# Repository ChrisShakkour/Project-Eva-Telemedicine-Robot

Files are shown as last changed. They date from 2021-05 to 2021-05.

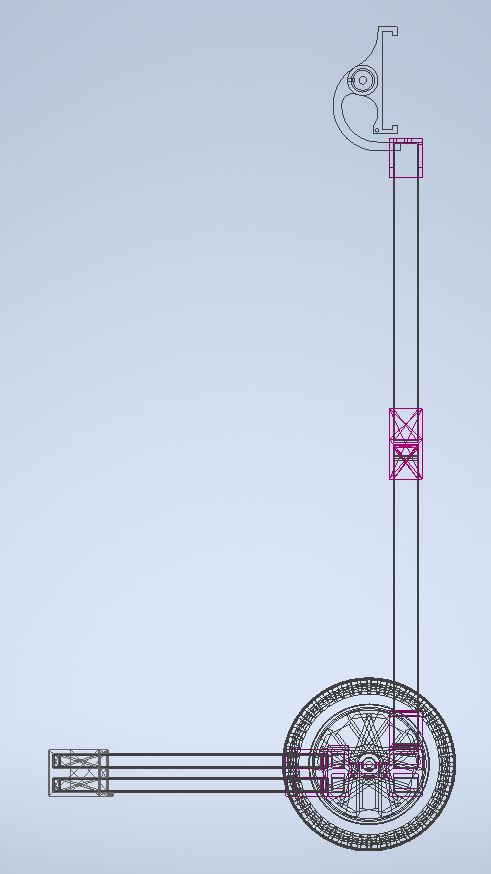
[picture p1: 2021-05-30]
Mechanical design/pictures/Capture2.JPG

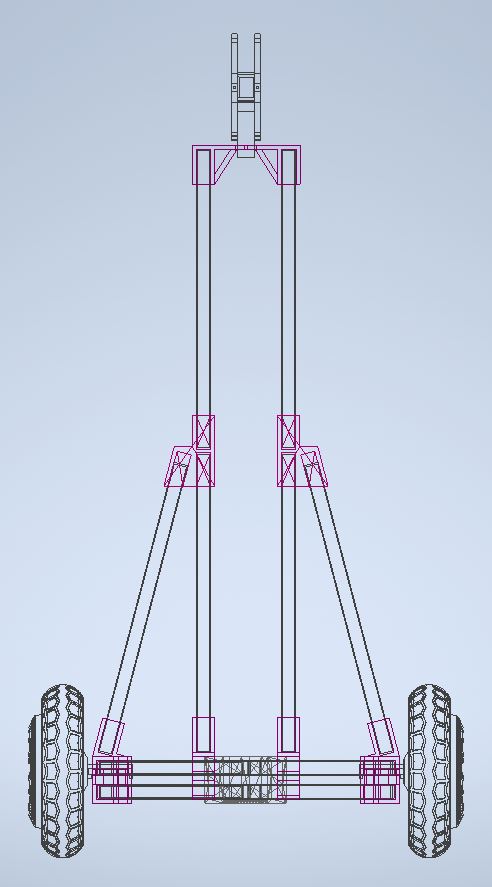
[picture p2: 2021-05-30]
Mechanical design/pictures/Capture1.JPG

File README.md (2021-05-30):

# Project Eva Telemedicine Robot

## Abstract
Telemedicine or Telehealth is the distribution of health-related services and information via 
electronic information and telecommunication technologies. It allows long-distance patient and 
clinician contact, care, advice, reminders, education, intervention, monitoring, and remote 
admissions. In this project we aim to build an easy to use, yet intelligent Robot assistant that will 
serve as a RC gateway between long distance patients and their families, doctors, loved ones
providing the patient with care, monitoring, & Telemedicine. The robot itself is a 3-wheel
differential drive robot built on a 3D printed chassis and a STM32F407VET microcontroller 
Featuring an Arm-Cortex-M4 168[MHz] Core. The robot is equipped with a mobile device 
(Tablet) to enable video conferencing. anyone with permissions can call the robot and remote 
control it from far away to monitor the patient/family member. The robot built in this project 
fully occupies these features, calling the robot from far away and driving in the patient’s home 
to firstly check on him and secondly check on his health and satisfaction, our conclusions from 
this robot are, firstly this concept could be implemented into a real life product with many use 
cases, secondly it is a product customers would like to use but don’t have the will to purchase 
because cheaper solutions can bring the same results at zero investment like using a 
smartphone to video conference, Etc.

## Project overview
Project EVA is a combination of 2 systems, an embedded real-time Robot system & an IoT 
software agent. the Robot system is independently handled with a microcontroller equipped 
with sensors, power distribution & management components, a camera, and an intelligent Real￾time software, whereas the IoT agent is built upon 2 applications running on different mobile 
devices connected via a firebase. The Robotic system receives commands from the IoT software 
agent via a Bluetooth wireless communication protocol.

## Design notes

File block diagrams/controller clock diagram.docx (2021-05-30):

Motor

Motor

BLDC motor drivers

BLDC motor drivers

PWM

PWM

Microcontroller

I2C

Capture compare

UART

SPI

Proximity sensors

Bluetooth module HC-05

Pixy camera

Accelerometer

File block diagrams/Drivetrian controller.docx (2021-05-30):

Left wheel speed

Right wheel speed

Radios of Arc

Speed

Drivetrain controller

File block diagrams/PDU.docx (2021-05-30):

Battery input voltage

14v-16.5v

PDU

Servo + proximity sensors circuit

Microcontroller

Pixy camera

14v-16.5v

5V

6V

BLDC Motor Driver

Min 14v

BLDC Motor Driver

Min 14v

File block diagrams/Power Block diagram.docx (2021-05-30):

14v-16v

6V

5V

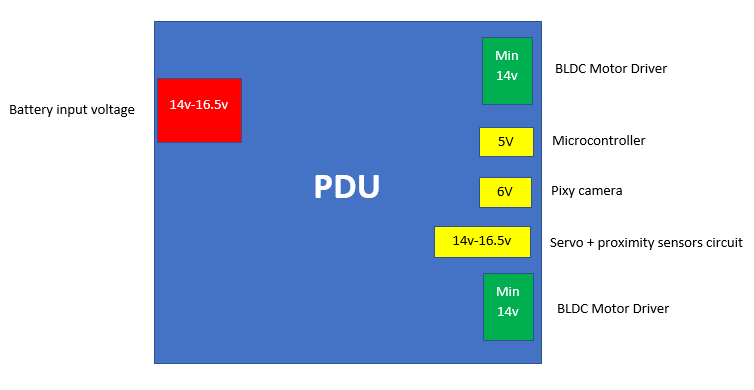
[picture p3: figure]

Sensory

Pixy Cam

Microcontroller

Power

BLDC motor driver

Power

BLDC motor driver

Battery 14v-16.5v

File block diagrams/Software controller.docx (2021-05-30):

Embedded Software controller

LWS

RWS

Speed

Radios

Gaussian transform

Speed

angle

Drivetrain controller

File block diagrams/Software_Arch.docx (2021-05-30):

External interrupt

Interrupt free

50ms

20ms

Bluetooth message handler

Kinematics controller

Scheduler

Main

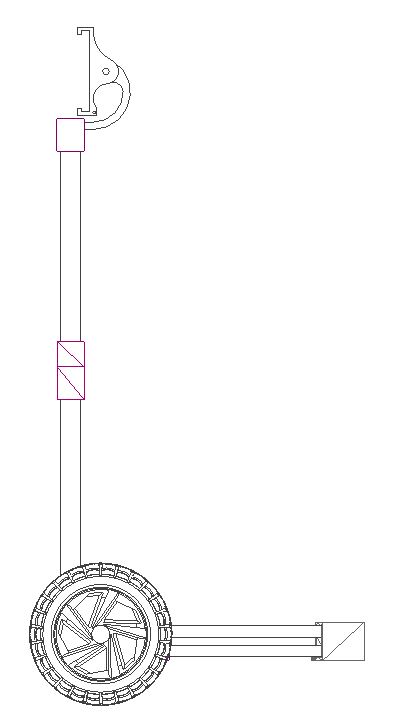
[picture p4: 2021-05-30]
Mechanical design/pictures/Capture10.JPG

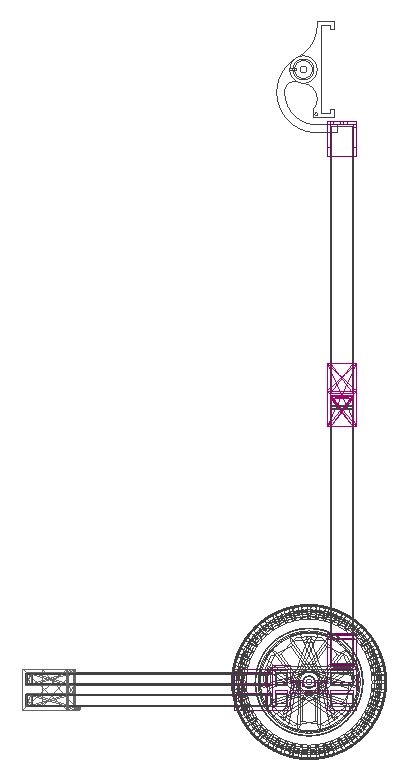
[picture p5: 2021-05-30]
Mechanical design/pictures/Capture5.JPG

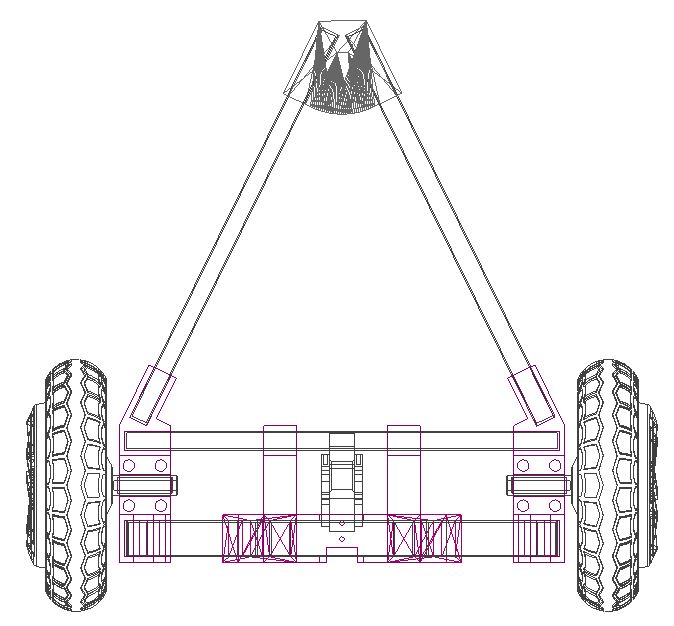
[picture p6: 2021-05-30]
Mechanical design/pictures/Capture7.JPG

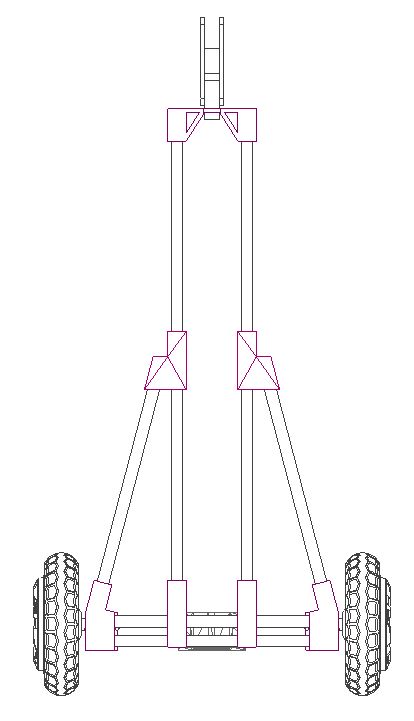
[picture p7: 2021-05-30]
Mechanical design/pictures/Capture12.JPG

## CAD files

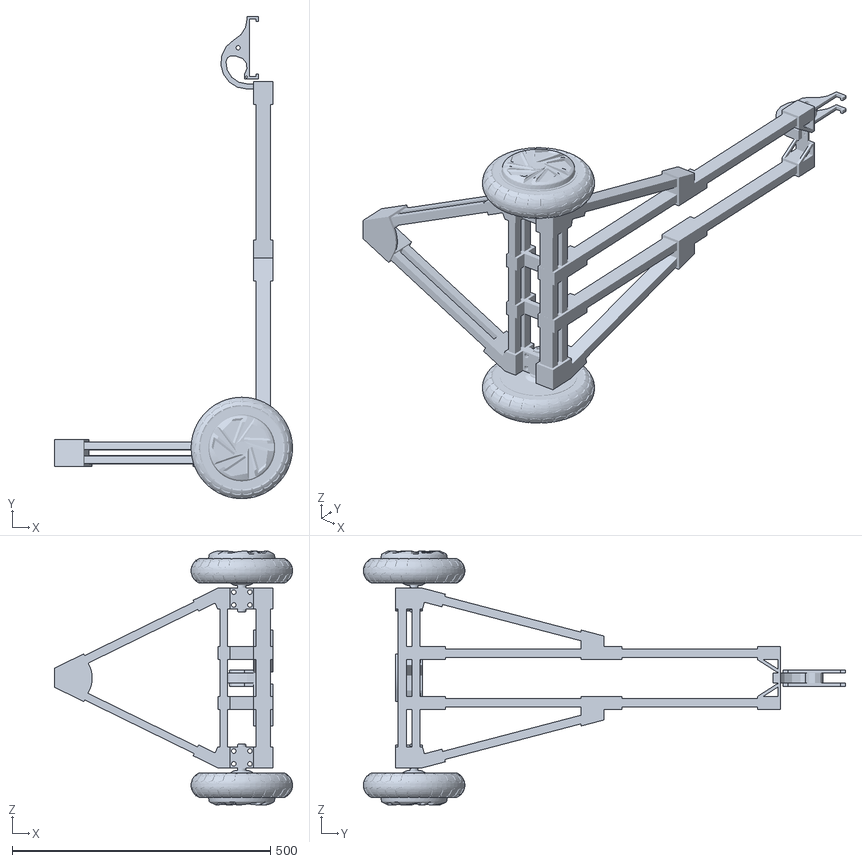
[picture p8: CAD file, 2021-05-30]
Mechanical design/Design sources/DriveTrain_Assembly.stl
461.3 x 934.3 x 492.2

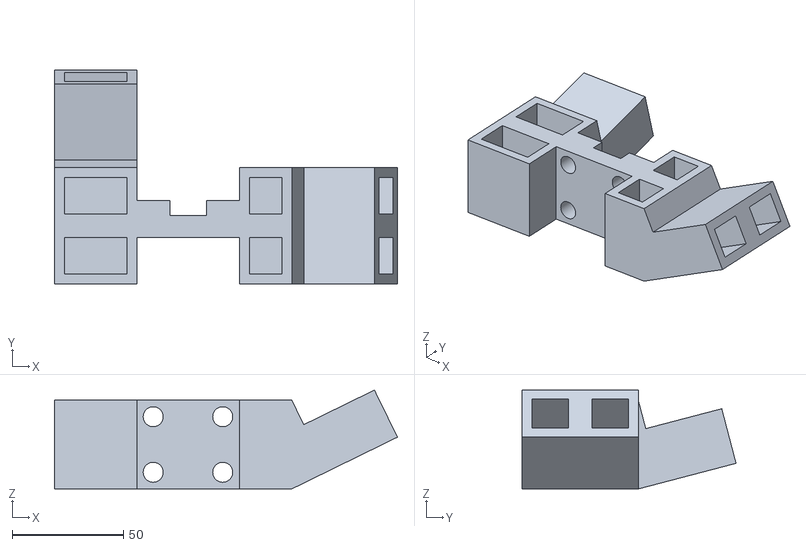
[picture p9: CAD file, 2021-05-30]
Mechanical design/Design sources/STL files/Right_front_Chasis_v2.stl
154.4 x 96.4 x 44.5

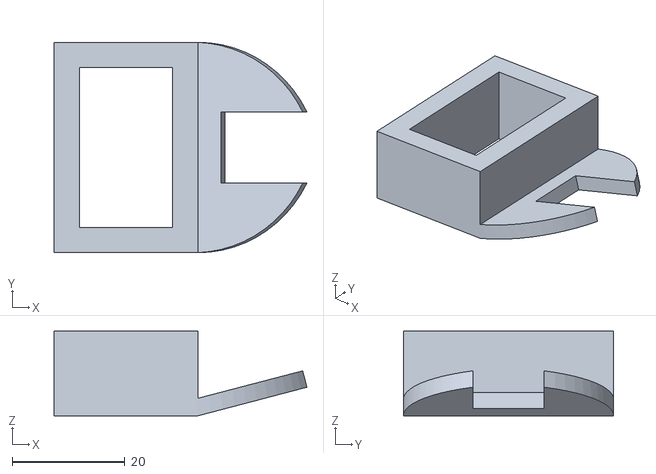
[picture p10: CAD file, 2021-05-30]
Mechanical design/Design sources/STL files/Servo front rightleft holder.stl
44.8 x 37.3 x 15.0

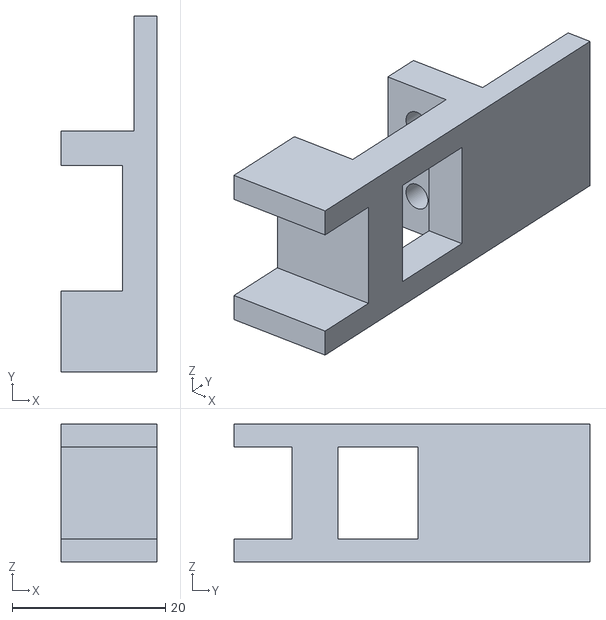
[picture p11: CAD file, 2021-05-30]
Mechanical design/Design sources/STL files/pixyCam_mount.stl
12.5 x 46.5 x 18.0

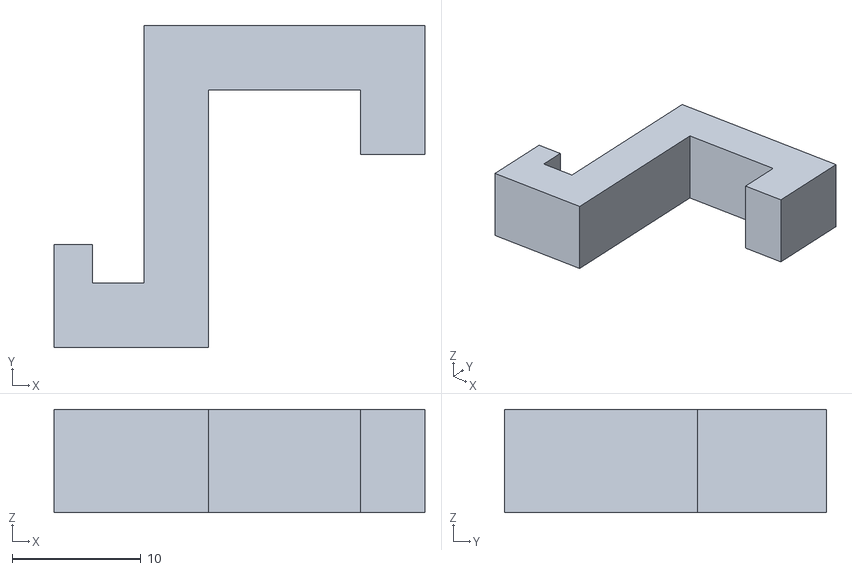
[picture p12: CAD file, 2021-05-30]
Mechanical design/Design sources/STL files/horizontal_clip.stl
28.8 x 25.0 x 8.00

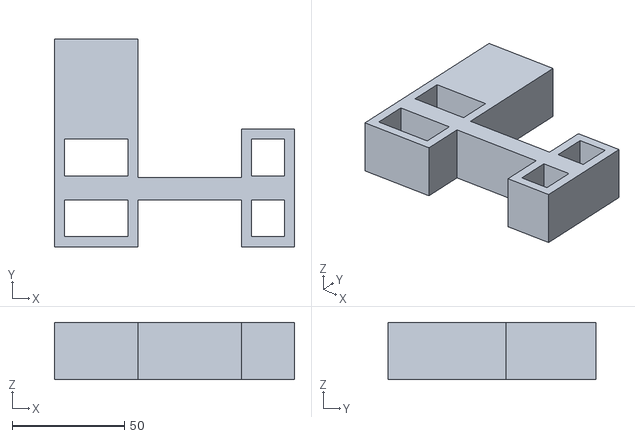
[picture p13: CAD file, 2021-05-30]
Mechanical design/Design sources/STL files/mid_front_Chasis.stl
106.8 x 92.4 x 25.4

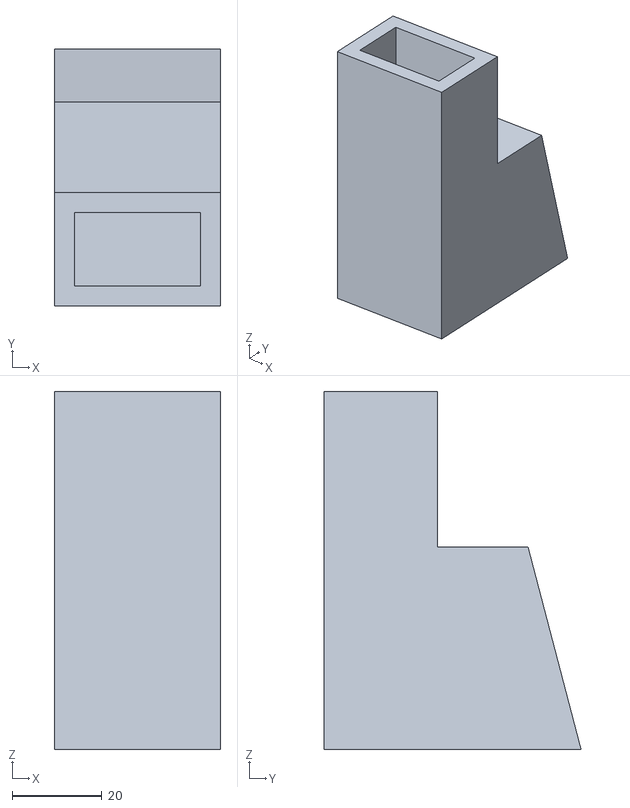
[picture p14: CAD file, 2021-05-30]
Mechanical design/Design sources/STL files/upper_joints.stl
37.2 x 57.5 x 80.0

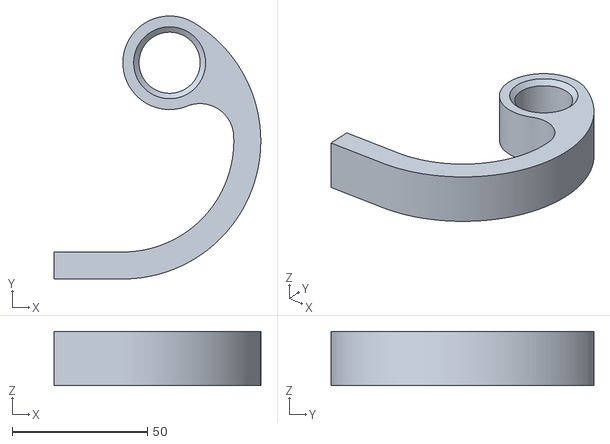
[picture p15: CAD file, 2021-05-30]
Mechanical design/Design sources/STL files/tablet_arm_joint.stl
76.4 x 97.3 x 20.0

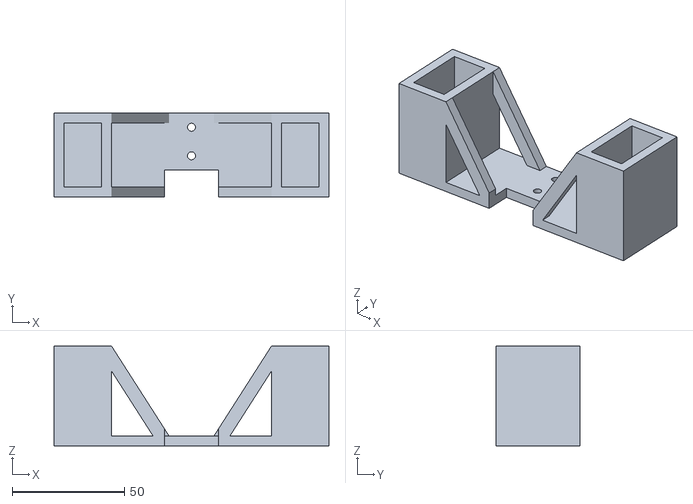
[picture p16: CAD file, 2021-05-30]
Mechanical design/Design sources/STL files/Tablet_joint_Holder.stl
122.4 x 37.4 x 44.5

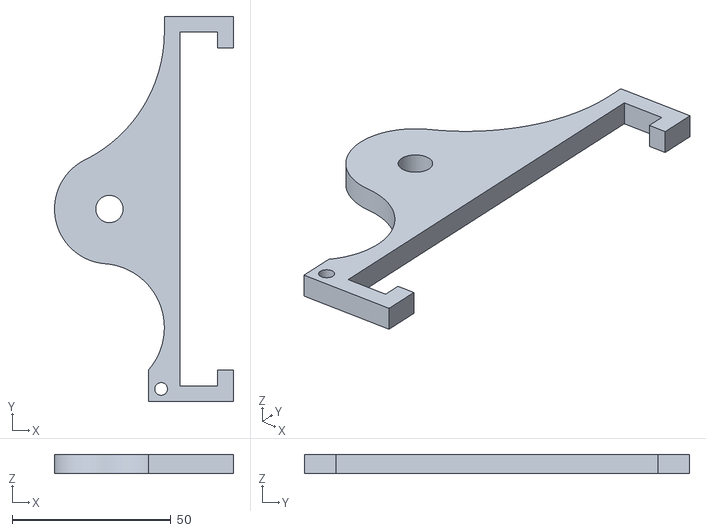
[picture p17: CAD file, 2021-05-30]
Mechanical design/Design sources/STL files/tab_clips.stl
56.4 x 121.4 x 6.00

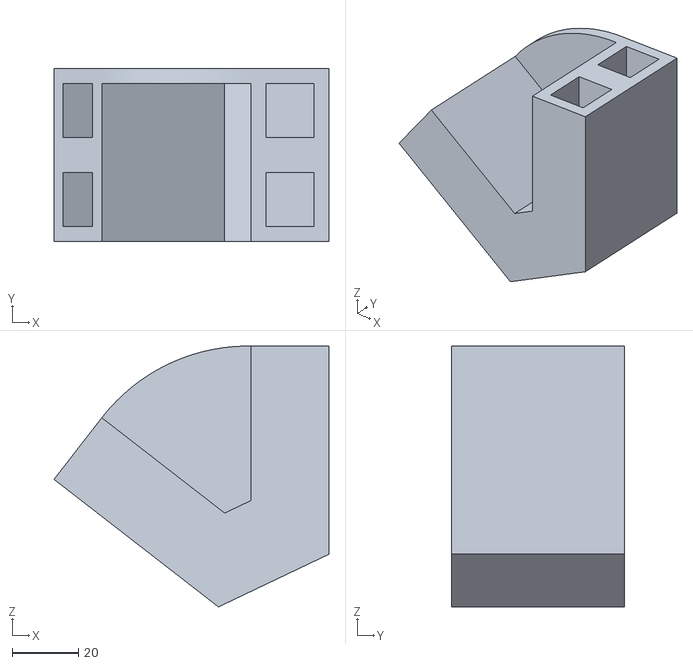
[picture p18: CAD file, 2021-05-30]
Mechanical design/Design sources/STL files/backwheel_Mount.stl
83.2 x 52.4 x 79.0

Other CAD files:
Mechanical design/Design sources/STL files/Left_front_Chasis_v2.stl
Mechanical design/Design sources/DriveTrain_Assembly.iam
Mechanical design/Design sources/Inventor files/Left_front_Chasis_v2.ipt
Mechanical design/Design sources/Inventor files/Motor_BLDC_Hoverboard_Wheel.ipt
Mechanical design/Design sources/Inventor files/PL_rod_double.ipt
Mechanical design/Design sources/Inventor files/PL_rod_single.ipt
Mechanical design/Design sources/Inventor files/Right_front_Chasis_v2.ipt
Mechanical design/Design sources/Inventor files/Servo front rightleft holder.ipt
Mechanical design/Design sources/Inventor files/Tablet_joint_Holder.ipt
Mechanical design/Design sources/Inventor files/backwheel.ipt
Mechanical design/Design sources/Inventor files/backwheel_Cap.ipt
Mechanical design/Design sources/Inventor files/backwheel_Mount.ipt
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

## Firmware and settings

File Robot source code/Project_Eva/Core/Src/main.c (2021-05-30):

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
/* Includes ------------------------------------------------------------------*/
#include "main.h"

I2C_HandleTypeDef hi2c2;

SPI_HandleTypeDef hspi1;

TIM_HandleTypeDef htim2;
TIM_HandleTypeDef htim3;
TIM_HandleTypeDef htim4;
TIM_HandleTypeDef htim6;
TIM_HandleTypeDef htim10;

UART_HandleTypeDef huart1;

void SystemClock_Config(void);
static void MX_GPIO_Init(void);
static void MX_TIM2_Init(void);
static void MX_I2C2_Init(void);
static void MX_SPI1_Init(void);
static void MX_USART1_UART_Init(void);
static void MX_TIM4_Init(void);
static void MX_TIM6_Init(void);
static void MX_TIM10_Init(void);
static void MX_TIM3_Init(void);
/* USER CODE BEGIN 0 */
	uint8_t inbuffer2[30] = {0};
	Pixy2_Data_CCC Signature_1;
	Pixy2_Data_LTC Barcode;
/* USER CODE END 0 */

/**
  * @brief  The application entry point.
  * @retval int
  */
int main(void)
{
  /* MCU Configuration--------------------------------------------------------*/

  /* Reset of all peripherals, Initializes the Flash interface and the Systick. */
  HAL_Init();

  /* Configure the system clock */
  SystemClock_Config();

  /* Initialize all configured peripherals */
  MX_GPIO_Init();
  MX_TIM2_Init();
  MX_I2C2_Init();
  MX_SPI1_Init();
  MX_USART1_UART_Init();
  MX_TIM4_Init();
  MX_TIM6_Init();
  MX_TIM10_Init();
  MX_TIM3_Init();
  /* USER CODE BEGIN 2 */
  calculate_Gaussian_Transform();
  //.set LED off:
  HAL_GPIO_WritePin(GPIOA, LED2_Pin, 0);
  //.general IO initializations:
  HAL_TIM_Base_Start_IT(&htim6);				//initiate scheduler timer 20ms period
  HAL_TIM_Base_Start_IT(&htim2);				//initiate Motor Drive control Timer 0.5ms period
  //.start UART Engine on interrupt mode:
  __HAL_UART_ENABLE_IT(&huart1, UART_IT_RXNE);	//initiate hsuart interrupt on rx

  //.setup MPU6050 Sensor:
  MPU6050_Init(&hi2c2);
  MPU_ConfigTypeDef MPU6050IMU ;
  MPU6050IMU.Accel_Full_Scale = AFS_SEL_2g;
  MPU6050IMU.CONFIG_DLPF = DLPF_184A_188G_Hz;
  MPU6050IMU.ClockSource = Internal_8MHz;
  MPU6050IMU.Gyro_Full_Scale = FS_SEL_250;
  MPU6050IMU.Sleep_Mode_Bit = 0;
  MPU6050_Config(&MPU6050IMU);
  RawData_Def Accel_Raw_Cali;
  MPU6050_Get_Accel_RawData(&Accel_Raw_Cali);
  // ************************
  Enable_Motor('R');
  Enable_Motor('L');
  Initiate_PWM_Signal('R');
  Initiate_PWM_Signal('L');
  Set_Right_Motor_Direction('F');
  Set_Left_Motor_Direction('F');

  HAL_TIM_PWM_Start(&htim3, TIM_CHANNEL_1);
  //HAL_TIM_PWM_Start(&htim3, TIM_CHANNEL_2);
  //HAL_TIM_PWM_Start(&htim3, TIM_CHANNEL_3);
  //HAL_TIM_PWM_Start(&htim3, TIM_CHANNEL_4);

  //htim3.Instance -> CCR1= (180+0)  ;
  //htim3.Instance -> CCR1= (180+90)  ;
  //htim3.Instance -> CCR1= (180+180)  ;
  //htim3.Instance -> CCR1= (180+45)  ;
  htim3.Instance -> CCR1= (180+180);
  //int num=360;
  /* USER CODE END 2 */

  /* Infinite loop */
  /* USER CODE BEGIN WHILE */
  while (1)
  {
    /* USER CODE END WHILE */

    /* USER CODE BEGIN 3 */
	  /*
	  for(int i=0; i<400; i++){
		  HAL_Delay(10);
		  htim3.Instance -> CCR1= (180+i);
	  }
	  for(int i=400; i>0; i--){
	  	  HAL_Delay(10);
	  	  htim3.Instance -> CCR1= (180+i);
	  }
	  */
  }
  /* USER CODE END 3 */
}

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
/* USER CODE BEGIN 4 */
void HAL_TIM_PeriodElapsedCallback(TIM_HandleTypeDef *htim){
//
	if( htim == &htim6 ){
		//Scheduler runs at 20ms
		scheduler();
	}
	if( htim == &htim2 ){
		//if(Halt_Controller == 0){
		Kinematics_Controler();
		//}
	}
}

void HAL_TIM_IC_CaptureCallback(TIM_HandleTypeDef *htim){
	HCSR06_Capture_Handler(htim);
}
//

/* USER CODE END 4 */
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


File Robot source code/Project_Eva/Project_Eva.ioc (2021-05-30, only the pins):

Mcu.UserName=STM32F407VETx
PA0-WKUP.GPIO_Label=Right_Mot_signal
PA0-WKUP.Signal=S_TIM2_CH1_ETR
PA1.GPIO_Label=Left_Mot_signal
PA1.Signal=S_TIM2_CH2
PA10.Signal=USART1_RX
PA4.GPIO_Label=R_Mot_EN
PA4.Signal=GPIO_Output
PA5.GPIO_Label=L_Mot_EN
PA5.Signal=GPIO_Output
PA6.GPIO_Label=LED1
PA6.Signal=GPIO_Output
PA7.GPIO_Label=LED2
PA7.Signal=GPIO_Output
PA8.GPIO_Label=Servo_EN
PA8.Signal=GPIO_Output
PA9.Signal=USART1_TX
PB10.Signal=I2C2_SCL
PB11.Signal=I2C2_SDA
PB3.Signal=SPI1_SCK
PB4.Signal=SPI1_MISO
PB5.Signal=SPI1_MOSI
PB7.GPIO_Label=SPI1_SS
PB7.Signal=GPIO_Output
PB8.Signal=S_TIM10_CH1
PC4.GPIO_Label=R_Mot_Dir
PC4.Signal=GPIO_Output
PC5.GPIO_Label=L_Mot_Dir
PC5.Signal=GPIO_Output
PC6.Signal=S_TIM3_CH1
PD12.Signal=S_TIM4_CH1
PD13.Signal=S_TIM4_CH2
PD14.Signal=S_TIM4_CH3
PD15.Signal=S_TIM4_CH4

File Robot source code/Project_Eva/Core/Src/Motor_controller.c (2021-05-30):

/*
 * Motor_controller.c
 *
 *  Created on: Oct 17, 2020
 *      Author: chris
 */

#include "main.h"

TIM_HandleTypeDef htim1;
TIM_HandleTypeDef htim2;
TIM_HandleTypeDef htim3;

uint8_t Threshold = upper_Threshold;
int prev_Throttle =0;

float l = Robot_Length/2;
float Target_speed =0;
float Right_Target_Speed =0;
float Left_Target_Speed =0;
float Right_Motor_Speed =0;
float Left_Motor_Speed =0;
char prev_Right_Wheel_dir = FORWARD;
char prev_Left_Wheel_dir = FORWARD;
char Right_Wheel_dir = FORWARD;
char Left_Wheel_dir = FORWARD;
float H_of_X[181];
int Polarity_Vector[4] = {1, -1, -1, 1};

/* calculates the discrete transformation vector
 * that transforms the user angle into a radius
 * of turning of the robot, this function runs
 * once after the Micro-controller is initialized.
 */
void calculate_Gaussian_Transform(){
//
	float F_of_X[4];
	for(int i=0; i<=90; i++){
		F_of_X[0] = a1*expf(-pow(i-b,2)/(2*pow(c1,2)));
		F_of_X[1] = a2*expf(-pow(i-b,2)/(2*pow(c2,2)));
		F_of_X[2] = a3*expf(-pow(i-b,2)/(2*pow(c3,2)));
		F_of_X[3] = a4*expf(-pow(i-b,2)/(2*pow(c4,2)));
		H_of_X [i] = F_of_X[0] + F_of_X[1] + F_of_X[2] + F_of_X[3];
		H_of_X [180-i] = H_of_X [i];
	}
}

int Get_Halt_Status(){
	int Halt=0;
	Halt += UART_Halt_Status();
	Halt += Scheduler_Halt_Status();
	return Halt;
}

//Runs at 0.5ms 1Khz
void Kinematics_Controler(){
//
	float Speed =0;
	int Joy_Angle =0;

	if(Get_Halt_Status() != HALT){
		if(Scheduler_Control()){
			Speed = get_Scheduler_Speed();
			Joy_Angle = get_Scheduler_Angle();
		}
		else if(Remote_Control() == ENABLED){
			Speed = Get_Gradiant_Trottle();
			Joy_Angle = get_angle();
		}
		else {
			//Speed = Get_SW_Speed();
			//Joy_Angle = Get_SW_Angle();
		}
	}
	else {
		Speed=0;
		Joy_Angle =0;
	}
	int polar = Joy_Angle/90;
	int ang = Joy_Angle%180;
	float Rad = 0;
	float diff =0;

	if(abs(Speed) <= Cutoff_speed) Speed =0;

	if(ang<20 || ang>160){
		Right_Target_Speed = -Speed*pitch_res*Polarity_Vector[polar];
		Left_Target_Speed  =  Speed*pitch_res*Polarity_Vector[polar];
	}
	else {
		if(Joy_Angle >= 180) Speed = -Speed;
		// ################### System Plant #####################
		/* calculate the desired wheel speeds
		 * right = Omega(Raduis-L/2) = V/R(R-L/2) = V(1-L/2R)
		 * Left  = Omega(Raduis+L/2) = V/R(R+L/2) = V(1+L/2R)*/
		Rad = H_of_X[ang]*Polarity_Vector[polar];
		diff = l/Rad;
		Right_Target_Speed = Speed*(1.0 - diff);
		Left_Target_Speed  = Speed*(1.0 + diff);
	}
	//Get_PID_Controller_Correction()
	float R_error = Right_Target_Speed - Right_Motor_Speed;
	float L_error = Left_Target_Speed - Left_Motor_Speed;
	Right_Motor_Speed += R_error*Kp;
	Left_Motor_Speed  += L_error*Kp;

	if(abs(Right_Motor_Speed) < Dir_Trans_Speed){
		Right_Wheel_dir = (Right_Motor_Speed>0)?FORWARD:BACKWARD;
		if(Right_Wheel_dir != prev_Right_Wheel_dir){
			Set_Right_Motor_Direction(Right_Wheel_dir);
			prev_Right_Wheel_dir = Right_Wheel_dir;
		}
	}
	if(abs(Left_Motor_Speed) < Dir_Trans_Speed){
		Left_Wheel_dir = (Left_Motor_Speed>=0)?FORWARD:BACKWARD;
		if(Left_Wheel_dir != prev_Left_Wheel_dir){
			Set_Left_Motor_Direction(Left_Wheel_dir);
			prev_Left_Wheel_dir = Left_Wheel_dir;
		}
	}
	//
	Set_Motor_Speed(RIGHT, abs(round(Right_Motor_Speed)));
	Set_Motor_Speed(LEFT, abs(round(Left_Motor_Speed)));
}

int Get_Gradiant_Trottle(){
//
	int Throttle = get_Throttle();
	//
	if(abs(Throttle - prev_Throttle) > joy_frame){
		if(Throttle > Threshold){
			Threshold = lower_Threshold;
			Target_speed = Throttle;
		}
		else {
			Threshold = upper_Threshold;
			Target_speed = 0;
		}
		prev_Throttle = Throttle;
	}
	//
	if(abs(Target_speed) <= Cutoff_speed) Target_speed =0;
	//
	return Target_speed;
}

void Enable_Motor(char motor){
//
	if(motor == RIGHT){
		HAL_GPIO_WritePin(GPIOA, R_Mot_EN_Pin, 0);
	}
	if(motor == LEFT){
		HAL_GPIO_WritePin(GPIOA, L_Mot_EN_Pin, 0);
	}
} //One is enabled

void Disable_Motor(char motor){
//
	if(motor == RIGHT){
		HAL_GPIO_WritePin(GPIOA, R_Mot_EN_Pin, 1);
	}
	if(motor == LEFT){
		HAL_GPIO_WritePin(GPIOA, L_Mot_EN_Pin, 1);
	}

} //Zero is Disabled

void Set_Right_Motor_Direction(char direction){
//
	if(direction == FORWARD){
		HAL_GPIO_WritePin(GPIOC, R_Mot_Dir_Pin, 1);	//forwards is 0
	}
	if(direction == BACKWARD){
		HAL_GPIO_WritePin(GPIOC, R_Mot_Dir_Pin, 0); //backwards is 1
	}

}

void Set_Left_Motor_Direction(char direction){
//
	if(direction == FORWARD){
		HAL_GPIO_WritePin(GPIOC, L_Mot_Dir_Pin, 0);	//forwards is 1
	}
	if(direction == BACKWARD){
		HAL_GPIO_WritePin(GPIOC, L_Mot_Dir_Pin, 1);	//backwards is 0
	}
}

void Set_Motor_Speed(char motor, uint8_t Speed){
//
	if(motor == RIGHT){
		htim2.Instance -> CCR1= Speed  ;
	}
	if(motor == LEFT){
		htim2.Instance -> CCR2= Speed  ;
	}
}

void Initiate_PWM_Signal(char motor){
//
	if(motor == RIGHT){
		HAL_TIM_PWM_Start(&htim2, TIM_CHANNEL_1);
	}
	if(motor == LEFT){
		HAL_TIM_PWM_Start(&htim2, TIM_CHANNEL_2);
	}
}

void Shutdown_PWM_Signal(char motor){
//
	if(motor == RIGHT){
		HAL_TIM_PWM_Stop(&htim2, TIM_CHANNEL_1);
	}
	if(motor == LEFT){
		HAL_TIM_PWM_Stop(&htim2, TIM_CHANNEL_2);
	}
}

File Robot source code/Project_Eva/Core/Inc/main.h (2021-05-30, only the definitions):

#define Right_Mot_signal_Pin GPIO_PIN_0
#define Right_Mot_signal_GPIO_Port GPIOA
#define Left_Mot_signal_Pin GPIO_PIN_1
#define Left_Mot_signal_GPIO_Port GPIOA
#define R_Mot_EN_Pin GPIO_PIN_4
#define R_Mot_EN_GPIO_Port GPIOA
#define L_Mot_EN_Pin GPIO_PIN_5
#define L_Mot_EN_GPIO_Port GPIOA
#define LED1_Pin GPIO_PIN_6
#define LED1_GPIO_Port GPIOA
#define LED2_Pin GPIO_PIN_7
#define LED2_GPIO_Port GPIOA
#define R_Mot_Dir_Pin GPIO_PIN_4
#define R_Mot_Dir_GPIO_Port GPIOC
#define L_Mot_Dir_Pin GPIO_PIN_5
#define L_Mot_Dir_GPIO_Port GPIOC
#define Servo_EN_Pin GPIO_PIN_8
#define Servo_EN_GPIO_Port GPIOA
#define SPI1_SS_Pin GPIO_PIN_7
#define SPI1_SS_GPIO_Port GPIOB

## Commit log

2021-05-30 Commit Project Data into github
    [DriveTrain_Assembly.iam, Left_front_Chasis_v2.ipt, Left_front_Chasis_v2.stl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]
2021-05-30 creating stl file for drivetrain assemble
    [DriveTrain_Assembly.stl]

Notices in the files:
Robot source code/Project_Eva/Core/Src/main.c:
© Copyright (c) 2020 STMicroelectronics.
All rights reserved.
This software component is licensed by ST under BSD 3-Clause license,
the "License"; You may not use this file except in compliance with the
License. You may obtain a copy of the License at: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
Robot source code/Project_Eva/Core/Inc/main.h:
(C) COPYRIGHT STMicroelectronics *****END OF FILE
